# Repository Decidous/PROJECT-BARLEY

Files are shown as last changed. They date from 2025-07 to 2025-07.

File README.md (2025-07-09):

# PROJECT: BARS



## Description
Project Barley, or B.A.R.S., short for Barangay Aerial Relief System, is a project that combines drones with the capabilities of GPS. In particular, the project is an autonomous, self-navigating drone using multiple sensors to reach a coordinate and return back home, all with one goal: to deliver relief packages of local places in need (AKA food, medical supplies, etc.). This project is my attempt to combine the resources currently available to autonomous vehicle designing on the internet, and companies like Zipline, to make my own version of an AUV. 

## The way it works is simple:
1. User packs a package in its fuselage, utilizing a disposable parachute to slow it’s decent to target coordinates
User uploads target coordinates
2. Drone is sent off, calculating a simple route towards the coordinates
3. After coordinates are reached, it’s hatches below open and perform a 180 clockwise fight reroute back home
4. Drone is caught with a net for simplicity sake
## Why I want to build it
* Project has been halted for a whole year
I started designing this project a year ago, but then I stopped because I was too focused on rocketry. I am focusing on this project again now because it has a lot of potential for real-world applications. 
* This tech is not very available around the world
Zipline is my biggest inspiration, but they have limited hubs. I’d like to simplify this technology a ton so that implementation of this drone in other countries is less of a burden. 
* I think aerospace is cool
Everything aerospace related is super interesting to me, and although I switched my major from aerospace engineering to chemistry, I still super like the industry’s challenges and what they strive to solve. This is a main reason why I do rocketry and is trying to expand on my experiences on the field.

# BOM ($63.99 total)
| Platform | Description | Price per listed lot | # of parts per listed lot | Lots to purchase | Final Price (CAD) | Final Price (USD) | Already Owned? | Comments | Link |
|---|---|---|---|---|---|---|---|---|---|
| (2x) SG90 Servo | Heavier, larger load servo type for wing flap control | $7.99 | 4 | 1 | 10.86 | 7.99 | yes | | [Link](https://www.amazon.com/Micro-Servos-Helicopter-Airplane-Controls/dp/B07MLR1498/ref=sr_1_6) |
| MG996R Servo Motor | Lighter, smaller load servo type for hatch control | $9.99 | 2 | 1 | 13.59 | 9.99 | yes | | [Link](https://www.amazon.com/AEDIKO-MG996R-Control-Digital-Helicopter/dp/B09BZ5955Z/ref=sr_1_3) |
| ESP32-WROOM | Wifi + Cloud capabilities for real-time location data | $11.99 | 3 | 1 | 16.03 | 11.99 | yes | | [Link](https://www.amazon.com/ESP-WROOM-32-Development-Dual-Mode-Microcontroller-Compatible/dp/B0D53M13NS) |
| NEO-6M GPS Module ZC323200 | Listens to GPS location + calculations | $8.99 | 2 | 1 | 12.23 | 8.99 | yes | | [Link](https://www.amazon.com/HiLetgo-GY-NEO6MV2-Controller-Ceramic-Antenna/dp/B01D1D0F5M) |
| Passive Buzzer CYT1008 | Emits sound for pre/post-flight procedures | $5.99 | 10 | 1 | 8.15 | 5.99 | yes | | [Link](https://www.amazon.com/Cylewet-Terminals-Electronic-Electromagnetic-Impedance/dp/B01NCOXB2Q/ref=sr_1_1) |
| BMP280 Barometer | Consistent Altitude reading | $5.99 | 5 | 1 | 8.15 | 5.99 | yes | | [Link](https://www.amazon.com/KOOBOOK-GY-BMP280-3-3-Precision-Atmospheric-Barometric/dp/B07S98QBTQ/ref=sr_1_1) |
| MPU6050 Accelerometer | Orientation calibration | $9.59 | 3 | 1 | 13.04 | 9.59 | yes | | [Link](https://www.amazon.com/EC-Buying-Accelerometer-Gyroscope-Module16-Bit/dp/B0B3D6D1KD/ref=sr_1_2) |
| Puffin Smart 4G LTE-Advanced USB WiFi | Utilizes a SIM card for 4G cellular communication to the ESP32 | $41.00 | 1 | 1 | 55.76 | 41.00 | no | | [Link](https://www.amazon.com/Puffin-Smart-LTE-Advanced-Dongle-Hotspot/dp/B0DSJZ8KVB/ref=sr_1_8) |
| GY-273 Magnetometer | Functions as a compass for 2D navigation | $7.99 | 2 | 1 | 10.87 | 7.99 | yes | | [Link](https://www.amazon.com/Comimark-QMC5883L-Compass-Magnetometer-Arduino/dp/B0855TZV1J/ref=sr_1_1) |
| A2212 Brushless Motor Propeller | 10 inch propellers | $9.99 | 2 | 1 | 13.59 | 9.99 | yes | | [Link](https://www.amazon.com/uxcell-Propellers-2-Vane-Airplane-Adapter/dp/B07YYV9Q2X/ref=sr_1_4) |
| Carbon Fiber tube | 20mm diameter, 1 meter long | $22.99 | 1 | 1 | 31.27 | 22.99 | no | | [Link](https://speedyfpv.com/products/1000mm-3k-carbon-fiber-tubes-16-18-20-25mm-matte-glossy-1mm-2mm-walls) |

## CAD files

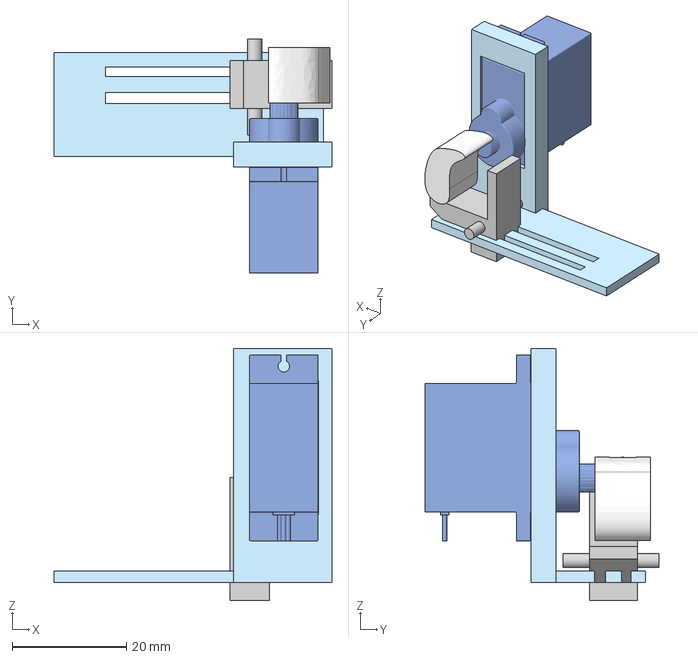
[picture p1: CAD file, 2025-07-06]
CAD/hatch_lock/hatch lock full assembly.step
48.6 x 41.0 x 44.1 mm

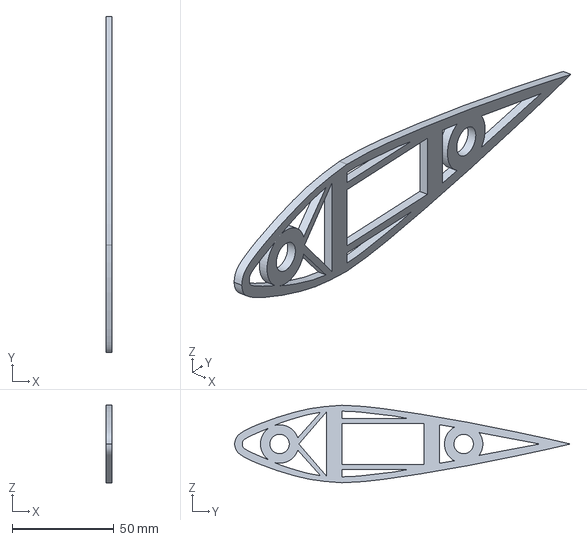
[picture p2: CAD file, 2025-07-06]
CAD/airframe/main wing cross section.step
3.00 x 165.1 x 38.1 mm

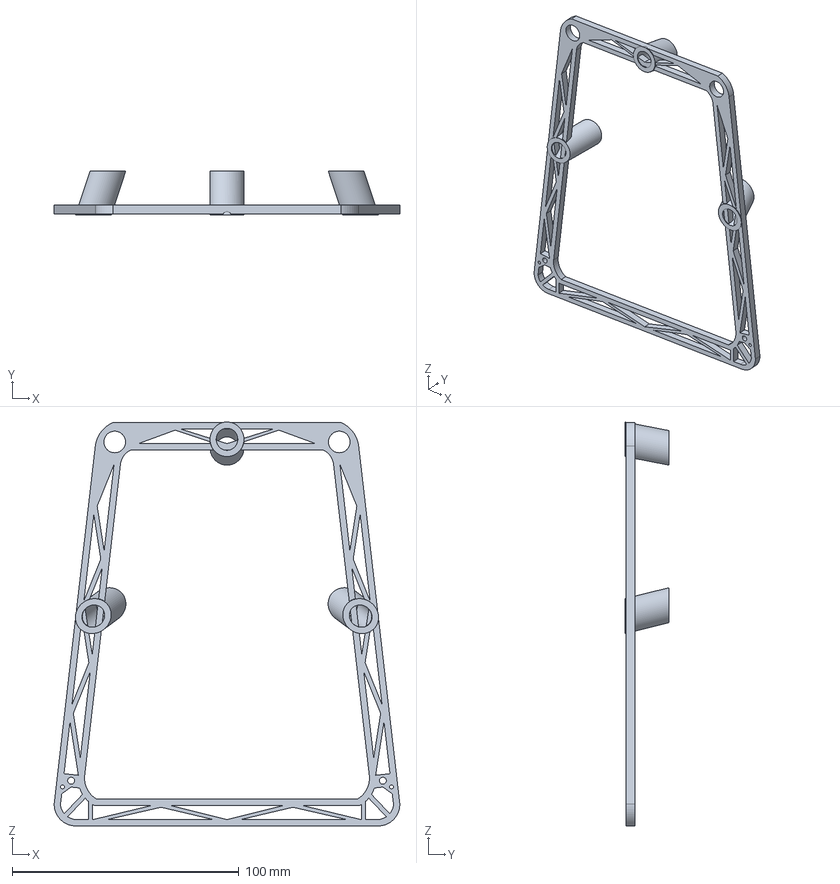
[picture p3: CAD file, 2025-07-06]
CAD/airframe/motor_mount_4.step
152.4 x 19.5 x 178.1 mm

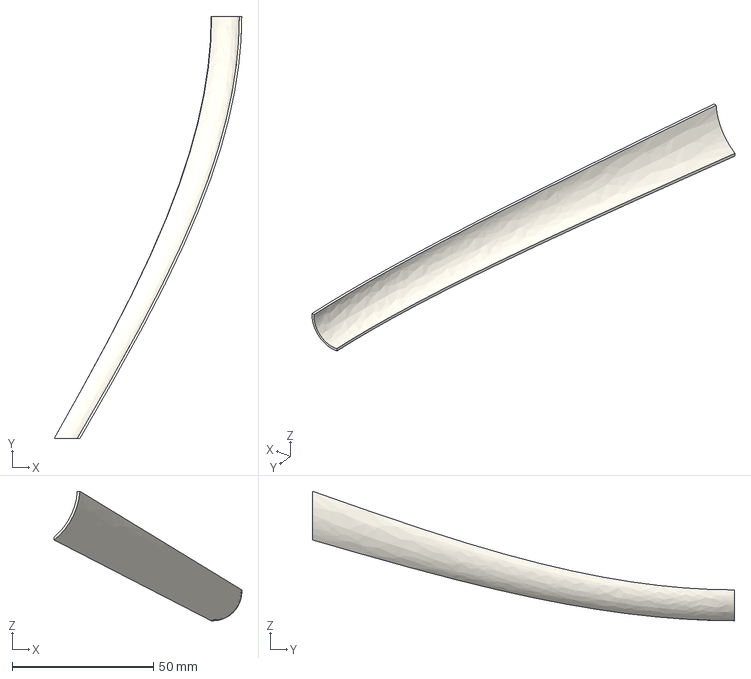
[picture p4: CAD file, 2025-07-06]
CAD/shells/shell_4.step
66.4 x 149.4 x 45.9 mm

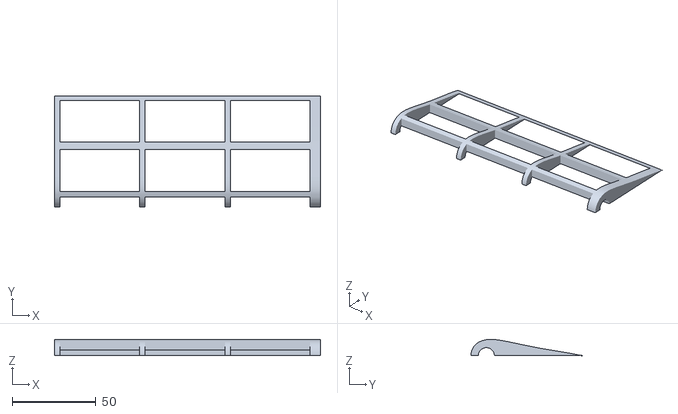
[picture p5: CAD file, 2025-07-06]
CAD/wing flaps v1.stl
158.8 x 66.4 x 9.73

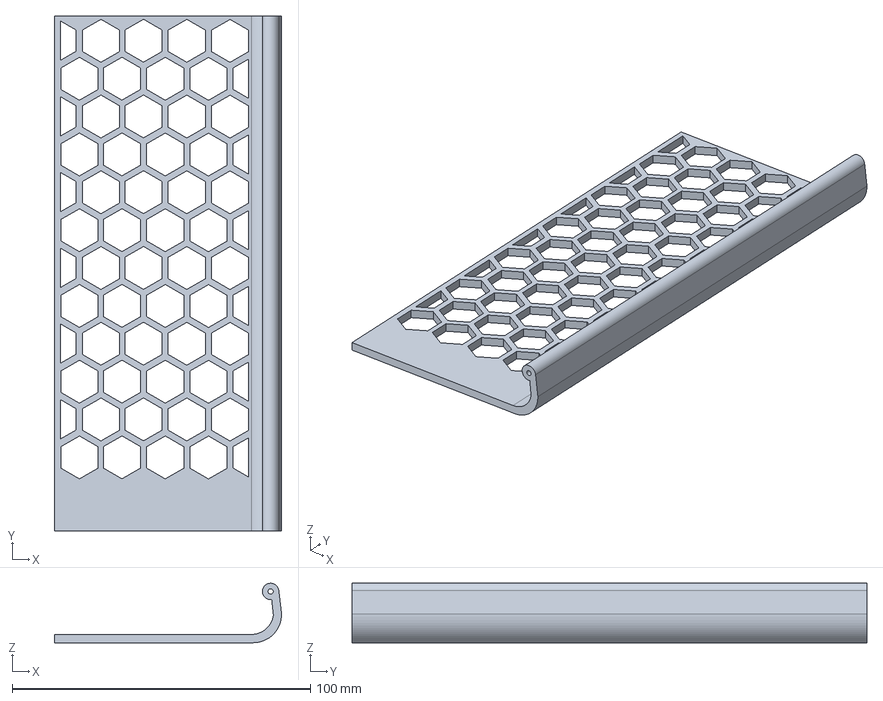
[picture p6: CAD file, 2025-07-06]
CAD/hatch_lock/pioneer gate.step
76.2 x 172.7 x 20.0 mm

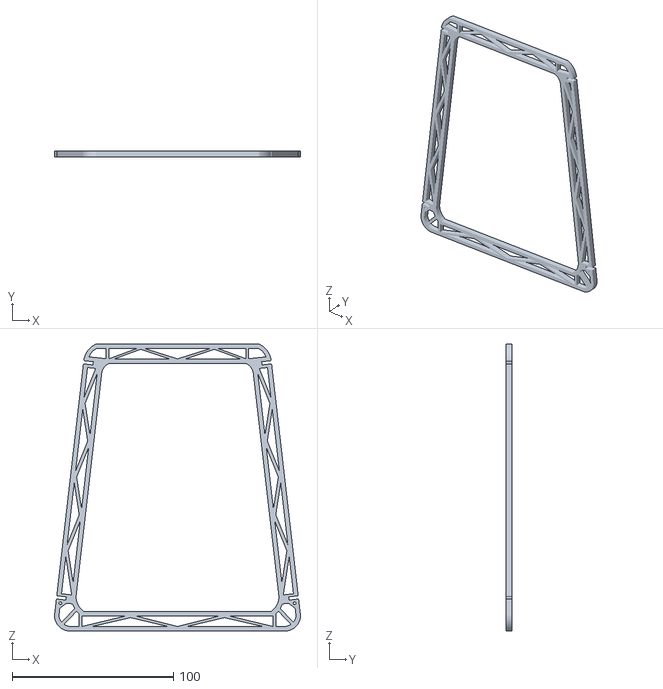
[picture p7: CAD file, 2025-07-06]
CAD/pioneer frame ribs.stl
152.4 x 4.00 x 177.8

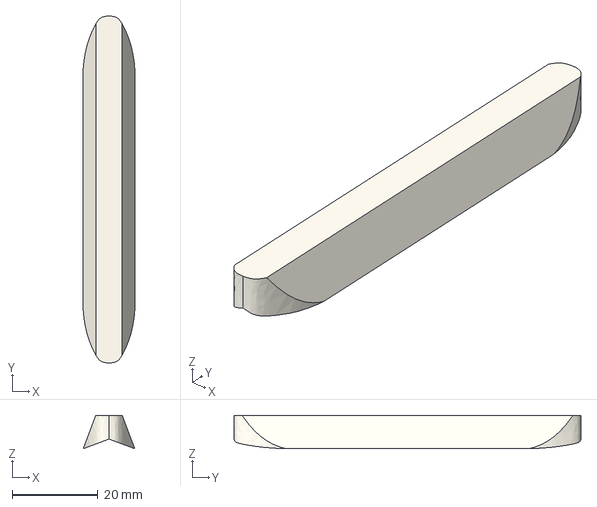
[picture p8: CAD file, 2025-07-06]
CAD/shells/tail light.step
12.0 x 80.7 x 7.78 mm

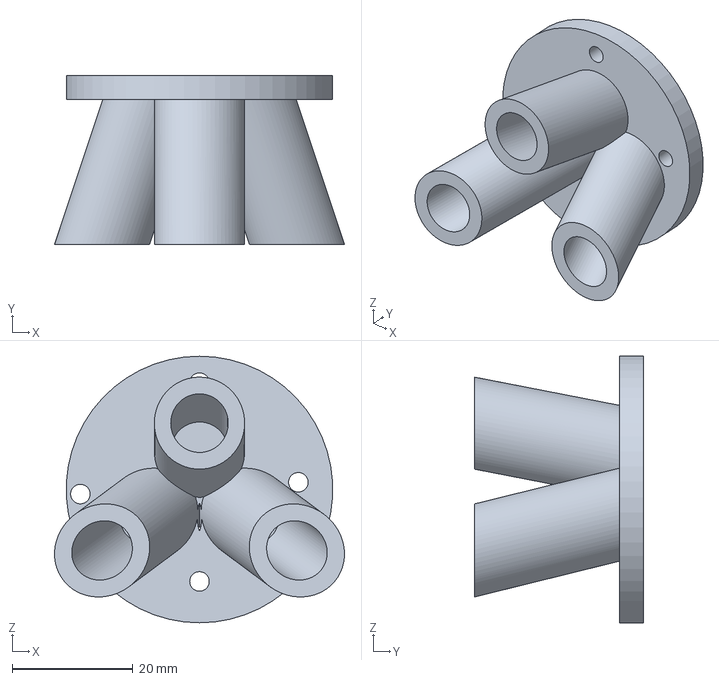
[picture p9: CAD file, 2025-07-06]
CAD/airframe/motor_mount_1.step
48.0 x 28.0 x 44.1 mm

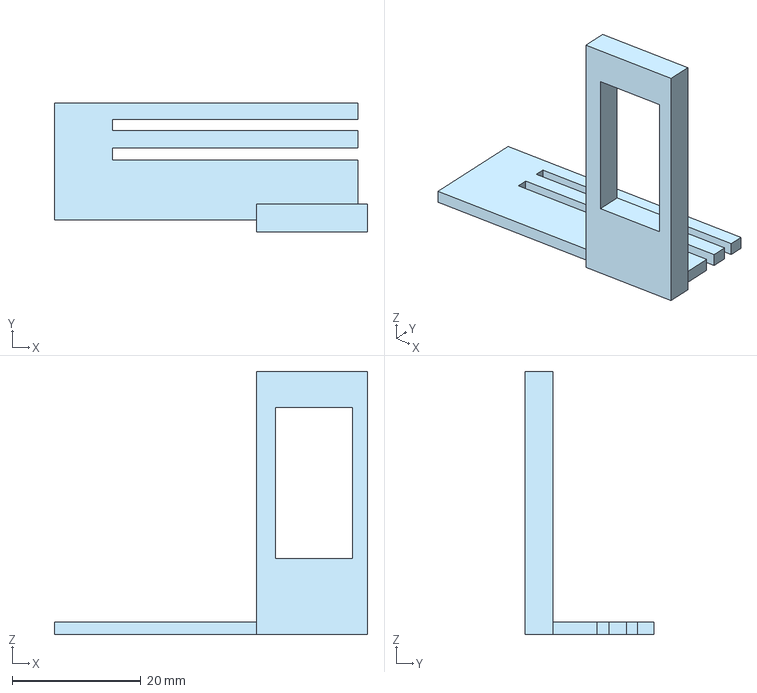
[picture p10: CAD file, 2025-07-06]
CAD/hatch_lock/hatchmount.step
48.6 x 20.0 x 40.9 mm

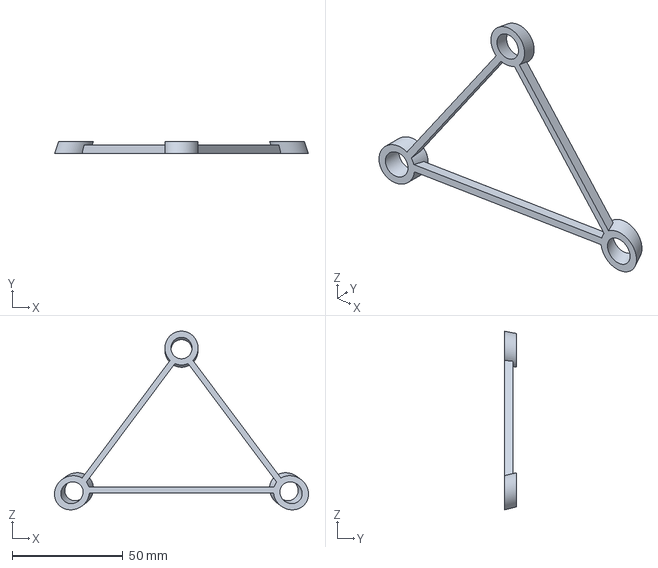
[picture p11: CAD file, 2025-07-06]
CAD/airframe/motor_mount_3.step
114.5 x 5.47 x 80.5 mm

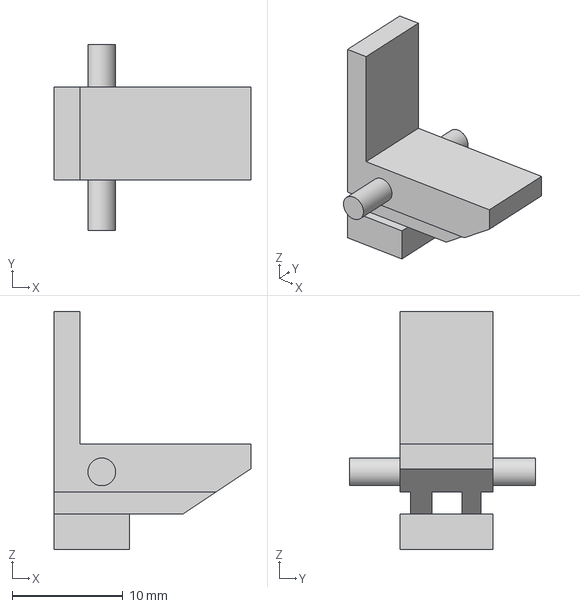
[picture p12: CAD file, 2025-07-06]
CAD/hatch_lock/hatchslide.step
17.8 x 16.8 x 21.5 mm

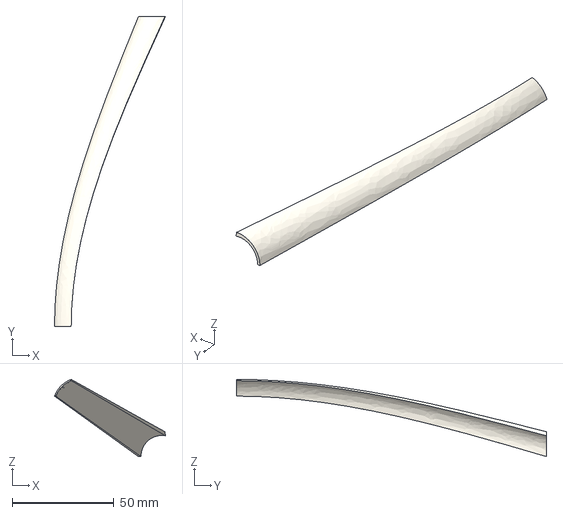
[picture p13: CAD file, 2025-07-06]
CAD/shells/shell_5.step
54.6 x 152.4 x 38.0 mm

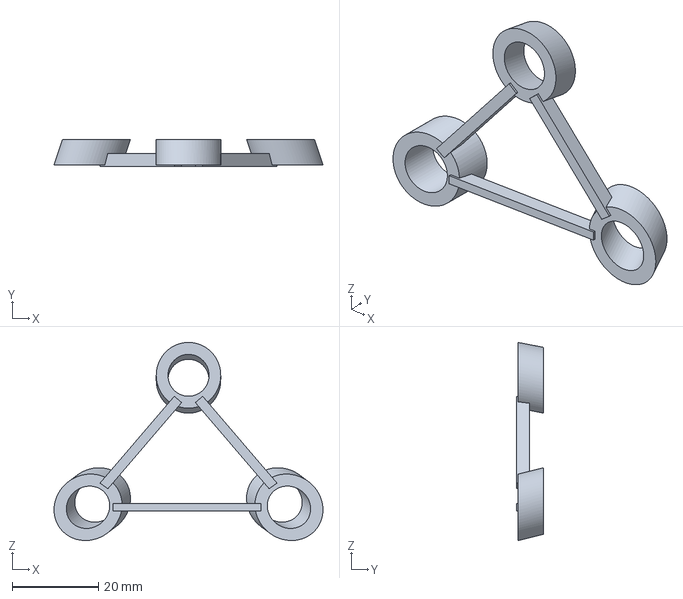
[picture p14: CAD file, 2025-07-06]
CAD/airframe/motor_mount_2.step
62.3 x 6.35 x 45.9 mm

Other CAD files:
CAD/shells/shell_3.step
CAD/shells/shell_1.step
CAD/airframe/airframe structure connection.step
CAD/shells/shell_8.step
CAD/shells/shell_2.step
CAD/shells/shell_6.step
CAD/shells/shell_7.step

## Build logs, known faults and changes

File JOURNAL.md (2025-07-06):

Title: "Project: BARS" <br>
Author: "Decidous" <br>
Description: "AUV capable of delivering packages via the use of GPS coordinates!" <br>
Created_at: "2025-06-27" <br>

# Total Time: 32 Hours
# 2025-06-28
Started this project amidst a vacation outside of the United States, so time available to work on this project is limited daily. Started part outsourcing: I started looking at the parts needed, but got only the main ones down (aka ESP32-WROOM, accelerometer + barometer + magnometer, etc) planning to continue the GPS/autonomous parts selection of this project some future date. These are the main components I usually use for my rocketry projects.
## Allotted time: 2 hours

# 2025-06-29
First instances of modeling, started with the ribs of the frame for the drone. I’ve decided to allocate a lot of space in Teh fuselage to fit packages 6 inches X 6 inches, and while this might not be a lot of space, it still contains the basic potential concept of delivering packages 

## allotted time: 2 hours

# 2025-06-30
I continued the modeling of the plane’s main airframe, and while doing some research, have decided that fiberglass is a fantastic middle ground of tensile strength and flexibility. I had 3 options from order of tensile strength and weight: aluminum, fiberglass, and carbon fiber. The availability of fiberglass rods I recalled from a ZNA video I watched a long time ago when he used it to make a bow and arrow.


https://www.youtube.com/watch?v=0XofhpYmaEU
## allotted time: 2 hours

# 2025-07-01
I continued with the designs of the different parts for the drone: the gates needed to hold the packages, the connectors connecting the fiberglass rods of the wings to the fuselage, and the wing profiles. The wing profile I currently have is called the symmetrical airfoil, which is supposed to be good for “precision aerobatics”. I am choosing this one also because it is the simplest to construct.
Flight test airfoil explanations: https://www.flitetest.com/articles/what-airfoil-should-i-use

## allotted time: 4 hours

# 2025-07-02
focused on combining everything together: the wing profiles, the gates, and the connectors. The paneling of the plane, I anticipate, would be made of Kraft foam to lessen the weight. For the nose and tail design, which were a bit more tricky, I designed only the corners to be 3d printed, but the centers of the nose and tail would still be filled with Kraft foam.

## allotted time: 3 hours

# 2025-07-03
Originally I had planned an H shape for the tail, but I did some research and the more V and /\ shapes (like the tail from the RQ-7 Shadow) you have in the front cross section of the plane, the better it is for aerodynamic self-leveling to correct for yaw drift. While yaw control would still be needed, this greatly lessens the strain of servos, leading to a potentially longer battery life and flight endurance. I finished modeling the wing flaps and added a tail light mount. I then struggled for a few hours trying to figure out how to mount the brushless motor in the aft end of the fuselage, I will definitely be coming back to the design because lofting is not ideal for angled pieces to hold fiberglass rods.
Study focusing on Dihedral Effects: https://journals.sagepub.com/doi/full/10.1155/2013/308582

## allotted time: 4 + 2 hours

# 2025-07-04
added color to assembly/fixed a few issues (dark = 3d printed framing, white = 3d printed shelling, orange = fiberglass rods for structure) + also researched more on GPS to focus on finalizing the BOM.
https://www.youtube.com/watch?v=F9lim5l9R7c -> GPS basic compass
https://www.youtube.com/watch?v=vi_cIuxDpcA&ab_channel=CircuitDigest -> sending to a cloud
## 5+ hours spent researching dif methods of wireless coms:
So, first I was thinking of using a wifi router + esp32, then realized i have no idea how internet works. I had to do a bunch of research to learn that the internet is basically provided via ethernet, and a wifi router serves as a well to that data. My challenge is that you need to be able to send data to a public server to track the location of the drone, and the methods to do that are:
1. cellular (with wifi -> https://www.youtube.com/watch?v=B96JGoWQOsE&t=1413s&ab_channel=Tesseract) 
2. Long-range radio (bps.space rocket telemetry -> https://www.youtube.com/watch?v=pZ572Rjj9vA&t=779s&ab_channel=BPS.space)
3. satelite data (wayyyy too expensive, but would work with ANY coordinate in the world)
4. sd card (simple hardware, but requires the drone to come back)
Cellular seems like the best bet due to its pretty good range (as long as there is a cell tower in proximity) as well as its affordability. Found a well-priced SIM 4G/5G modem that can be used to transmit data: "Puffin Smart 4G LTE-Advanced USB WiFi"

Also, finished a wiring schematic for the avionics:

## allotted time: 7 hours

# 2025-07-05
Made adjustments to motor mount for tail, door hatch servo system for deploying disaster relief supplies, finalized 3d model and finished up shelling, added models for servo and brushless motor



## allotted time: 6 hours

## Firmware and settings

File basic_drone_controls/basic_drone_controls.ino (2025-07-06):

#include <Servo.h>
#include <Wire.h>
#include <MPU6050.h>
#include <HardwareSerial.h>
#include <TinyGPS++.h>
#include <math.h>

#define HMC5883L_ADDRESS 0x1E // I2C address for HMC5883L

Servo myServo;
MPU6050 mpu;
TinyGPSPlus gps;
HardwareSerial GPSserial(1);

int buzzerPin = 2;

float pitch = 0;
unsigned long lastTime = 0;

// target coordinates
const float targetLat = 37.7749;   // example: perris california house address idk
const float targetLon = -122.4194;

void setup() {
  Serial.begin(115200);
  GPSserial.begin(9600, SERIAL_8N1, 16, 17);
  Wire.begin(21, 22);  // ESP32 I2C pins

  mpu.initialize();
  if (!mpu.testConnection()) {
    Serial.println("MPU6050 connection failed");
    while (1);
  }
  
  myServo.attach(27);
  myServo.write(90); // Start centered
  
  // Initialize HMC5883L magnetometer
  Wire.beginTransmission(HMC5883L_ADDRESS);
  Wire.write(0x00);
  Wire.write(0x70);
  Wire.endTransmission();

  Wire.beginTransmission(HMC5883L_ADDRESS);
  Wire.write(0x01);
  Wire.write(0xA0);
  Wire.endTransmission();

  Wire.beginTransmission(HMC5883L_ADDRESS);
  Wire.write(0x02);
  Wire.write(0x00);
  Wire.endTransmission();

  // Startup buzzer tones
  tone(buzzerPin, 400, 80);
  delay(80);
  noTone(buzzerPin);
  tone(buzzerPin, 500, 80);
  delay(80);
  noTone(buzzerPin);
  tone(buzzerPin, 600, 80);
  delay(80);
  noTone(buzzerPin);
  delay(1000);
  tone(buzzerPin, 800, 120);

  lastTime = millis();
}

void loop() {
  // 1. Read magnetometer data and calculate heading
  int16_t mx, my, mz;
  Wire.beginTransmission(HMC5883L_ADDRESS);
  Wire.write(0x03);
  Wire.endTransmission();
  Wire.requestFrom(HMC5883L_ADDRESS, 6);
  float heading = -1;
  if (Wire.available() == 6) {
    mx = Wire.read() << 8 | Wire.read();
    mz = Wire.read() << 8 | Wire.read();
    my = Wire.read() << 8 | Wire.read();
    heading = atan2(my, mx) * 180.0 / PI;
    if (heading < 0) heading += 360;
    Serial.print("Heading: ");
    Serial.println(heading);
  }

  // 2. Read MPU6050 pitch (optional, you can use this if needed for servo stabilization)
  int16_t ax, ay, az, gx, gy, gz;
  mpu.getMotion6(&ax, &ay, &az, &gx, &gy, &gz);
  float axg = ax / 16384.0;
  float azg = az / 16384.0;
  float gyRate = gy / 131.0;
  float pitchAcc = atan2(-axg, azg) * 180.0 / PI;
  unsigned long now = millis();
  float dt = (now - lastTime) / 1000.0;
  lastTime = now;
  pitch = 0.98 * (pitch + gyRate * dt) + 0.02 * pitchAcc;
  Serial.print("Pitch: ");
  Serial.println(pitch);

  // 3. Read GPS data
  while (GPSserial.available() > 0) {
    gps.encode(GPSserial.read());
  }

  if (gps.location.isUpdated()) {
    float droneLat = gps.location.lat();
    float droneLon = gps.location.lng();
    Serial.print("GPS Lat: "); Serial.println(droneLat, 6);
    Serial.print("GPS Lon: "); Serial.println(droneLon, 6);

    // 4. Calculate bearing to target
    float bearingToTarget = calculateBearing(droneLat, droneLon, targetLat, targetLon);
    Serial.print("Bearing to target: ");
    Serial.println(bearingToTarget);

    // 5. Calculate difference between target bearing and current heading
    float angleDiff = bearingToTarget - heading;

    // Normalize angle difference to range -180 to +180
    if (angleDiff > 180) angleDiff -= 360;
    if (angleDiff < -180) angleDiff += 360;

    Serial.print("Angle difference: ");
    Serial.println(angleDiff);

    // 6. Map angle difference to servo angle (example: center = 90)
    // Adjust mapping as per your servo orientation and drone setup
    int servoAngle = map(angleDiff, -180, 180, 0, 180);
    servoAngle = constrain(servoAngle, 0, 180);
    myServo.write(servoAngle);
  }

  delay(200); // Adjust delay as needed
}

// --- Bearing calculation function ---
float deg2rad(float deg) {
  return deg * PI / 180.0;
}

float rad2deg(float rad) {
  return rad * 180.0 / PI;
}

float calculateBearing(float lat1, float lon1, float lat2, float lon2) {
  float dLon = deg2rad(lon2 - lon1);
  lat1 = deg2rad(lat1);
  lat2 = deg2rad(lat2);

  float y = sin(dLon) * cos(lat2);
  float x = cos(lat1) * sin(lat2) - sin(lat1) * cos(lat2) * cos(dLon);

  float brng = atan2(y, x);
  brng = rad2deg(brng);
  brng = fmod((brng + 360.0), 360.0); // Normalize to 0-360

  return brng;
}

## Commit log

2025-07-06 new cad stuff
    [Project Barley Parts List - Sheet1 (3).csv, airframe structure connection.step, hatch lock full assembly.step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]
2025-07-06 added schematics
    [Project Barley Parts List - Sheet1 (3).csv, bars_wiring.kicad_sch]
2025-07-09 new BOM
    [Project Barley Parts List - Sheet1 (3).csv, Project Barley Parts List - Sheet1 (4).csv]
2025-07-09 changed BOM
    [Project Barley Parts List - Sheet1 (6).csv]
